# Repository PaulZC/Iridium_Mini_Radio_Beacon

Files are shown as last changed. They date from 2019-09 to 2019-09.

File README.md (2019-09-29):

# Iridium_Mini_Radio_Beacon

An 80g version of the [Iridium 9603N Beacon](https://github.com/PaulZC/Iridium_9603_Beacon) with eRIC4/9 radio support
.

Suitable for high altitude ballooning and many other asset tracking applications.

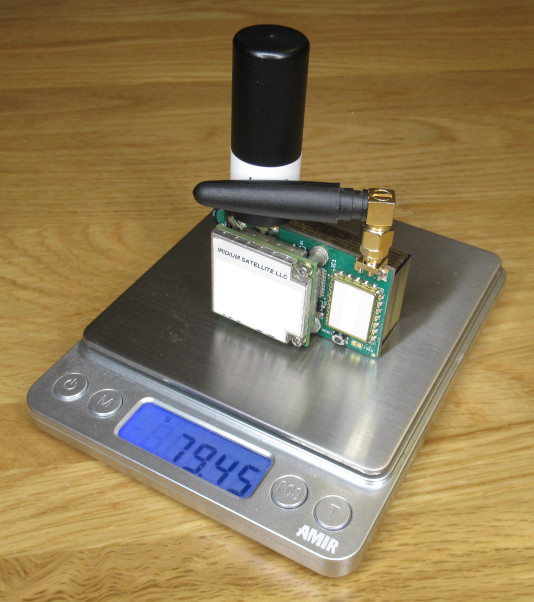
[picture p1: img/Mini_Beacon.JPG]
Mini_Beacon


This version is powered by a single Energiser® Ultimate Lithium L522 (PP3) 9V battery, which helps keep the design as compact as possible.

If you want to keep the size and weight as low as possible, and don't need a radio link, have a look at
the [Iridium 9603N Mini Beacon](https://github.com/PaulZC/Iridium_9603N_Mini_Beacon) instead.

The Iridium 9603N transceiver and u-blox MAX-M8Q GNSS receiver share a single Maxtena M1600HCT-P-SMA antenna, again to keep the weight as low as possible.
The antenna sharing circuit has been flight tested on the [Iridium 9603N Solar Beacon](https://github.com/PaulZC/Iridium_9603N_Solar_Beacon).

Full details of how to track your beacon via the Rock7 RockBLOCK Gateway are included in the
[Iridium 9603N Beacon repo](https://github.com/PaulZC/Iridium_9603_Beacon/blob/master/RockBLOCK.md).

[ASSEMBLY.md](https://github.com/PaulZC/Iridium_Mini_Radio_Beacon/blob/master/ASSEMBLY.md) describes how to assemble the PCB.

The [Arduino folder](https://github.com/PaulZC/Iridium_Mini_Radio_Beacon/tree/master/Arduino) contains the code for the SAMD21 processor.
You can find the [programming instructions](https://github.com/PaulZC/Iridium_9603_Beacon/blob/master/LEARN.md#how-do-i-install-the-atsamd21g18-bootloader)
and [upload instructions](https://github.com/PaulZC/Iridium_9603_Beacon/blob/master/LEARN.md#how-do-i-upload-the-arduino-code) in the Iridium 9603N Beacon repo.

The Eagle files are available in the [Eagle folder](https://github.com/PaulZC/Iridium_Mini_Radio_Beacon/tree/master/Eagle).

The schematic, dimensions and BOM are available [here](https://github.com/PaulZC/Iridium_Mini_Radio_Beacon/blob/master/Iridium_Mini_Radio_Beacon.pdf).

The [OpenSCAD folder](https://github.com/PaulZC/Iridium_Mini_Radio_Beacon/tree/master/OpenSCAD) contains .scad and .stl files for the 3D-printed cover.

## Licence

This project is distributed under a Creative Commons Attribution + Share-alike (BY-SA) licence.
Please refer to section 5 of the licence for the "Disclaimer of Warranties and Limitation of Liability".

Enjoy!

**_Paul_**

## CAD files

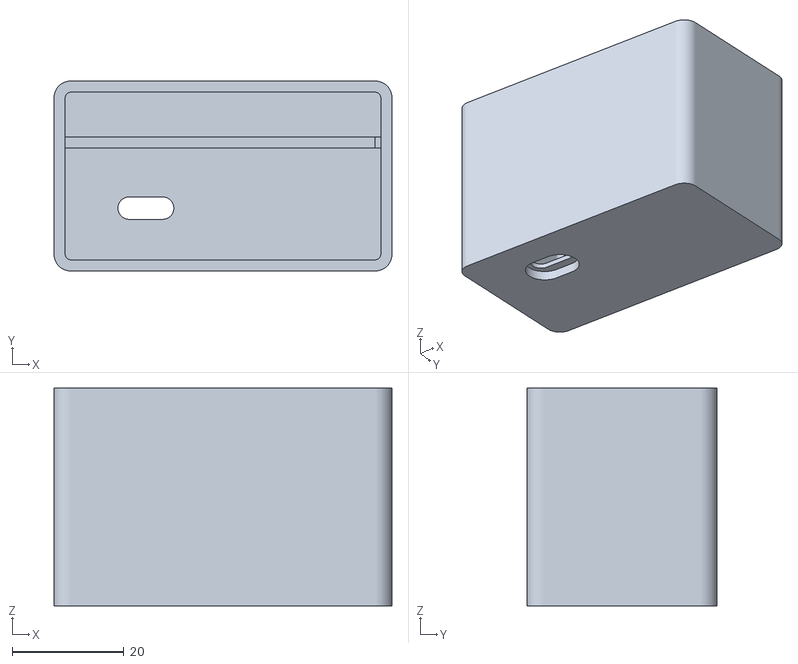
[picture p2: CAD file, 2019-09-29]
OpenSCAD/Mini_Radio_Beacon_Cover.stl
60.5 x 34.0 x 39.0

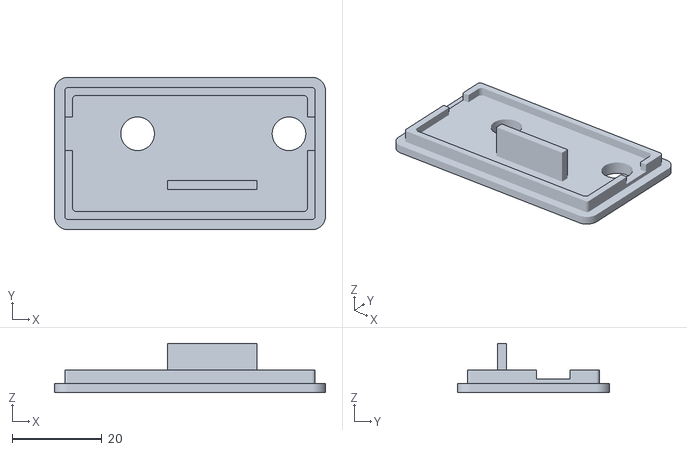
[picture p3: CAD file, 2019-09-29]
OpenSCAD/Mini_Radio_Beacon_Lid.stl
60.5 x 34.0 x 11.0

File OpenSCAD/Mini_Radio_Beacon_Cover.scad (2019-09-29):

// Simple Cover for the Iridium Mini Radio Beacon with USB opening

$fn=90; // fragments
wall = 2.0; // wall thickness
end_wall = 3.0; // end wall thickness
internal_width = 56.5; // internal width (X) of the cover
internal_depth = 30.0; // internal depth (Y) of the cover
internal_height = 35.0; // internal height (Z) of the cover
lid_insert = 1.0; // extra height for the lid insert

battery_support_height = 1.0; // Height (Z) of the battery support above the floor
battery_support_depth = 2.0; // Depth (Y) of the battery support
battery_support_offset = 5.0; // Y offset of the battery support

battery_support_2_width = 1.0; // Width (X) of the battery support from the wall
battery_support_2_height = 27.0; // Internal height (Z) of the battery support

internal_corner_radius = 1.0; // radius of the internal corner cylinder

usb_r = 2.0; // radius of the opening for the USB connector
usb_width = 10.0; // total width of the opening for the USB
usb_height = 1.0; // thickness of the opening for the USB connector
usb_recess_r = 4.0; // radius of the recess for the USB connector body
usb_recess_width = 12.0; // total width of the recess for the USB connector body
usb_x_offset = -13.8; // X offset of the USB connector
usb_y_offset = 5.75; // y offset of the USB connector

height = internal_height + end_wall + lid_insert; // cover external height (Z)
width = internal_width + (2 * wall); // cover external width (X)
depth = internal_depth + (2 * wall); // cover external depth (Y)

external_corner_radius = internal_corner_radius + wall; // external corner radius

module cover()
{
    translate([external_corner_radius, external_corner_radius, 0])
        minkowski() {
            cube([(width - (2 * external_corner_radius)), (depth - (2 * external_corner_radius)), (height / 2)]);
            cylinder(h=(height / 2), r=external_corner_radius);
        }
}

module void()
// Void will be higher than required to avoid zero thickness skin across opening
{
    translate([external_corner_radius, external_corner_radius, end_wall])
        minkowski() {
            cube([(internal_width - (2 * internal_corner_radius)), (internal_depth - (2 * internal_corner_radius)), (height / 2)]);
            cylinder(h=(height / 2), r=internal_corner_radius);
        }
}

module usb_opening_end_1()
// Cylinder is taller than it needs to be to avoid zero thickness skins
{
    translate([((usb_width / 2) - usb_r),0,usb_height]) {
        cylinder(h=end_wall,r=usb_r);
    }
}

module usb_opening_end_2()
// Cylinder is taller than it needs to be to avoid zero thickness skins
{
    translate([(0-((usb_width / 2) - usb_r)),0,usb_height]) {
        cylinder(h=end_wall,r=usb_r);
    }
}

module usb_opening_mid()
// Cube is taller than it needs to be to avoid zero thickness skins
{
    translate([(-0.5 * (usb_width - (2 * usb_r))), (-0.5 * (2 * usb_r)), usb_height]) {
        cube([(usb_width - (2 * usb_r)), (2 * usb_r), end_wall]);
    }
}

module usb_recess_end_1()
// Cylinder is taller than it needs to be to avoid zero thickness skins
{
    translate([((usb_recess_width / 2) - usb_recess_r), 0, (0 - usb_height)]) {
        cylinder(h=end_wall, r=usb_recess_r);
    }
}

module usb_recess_end_2()
// Cylinder is taller than it needs to be to avoid zero thickness skins
{
    translate([(0-((usb_recess_width / 2) - usb_recess_r)), 0, (0 - usb_height)]) {
        cylinder(h=end_wall, r=usb_recess_r);
    }
}

module usb_recess_mid()
// Cube is taller than it needs to be to avoid zero thickness skins
{
    translate([(-0.5 * (usb_recess_width - (2 * usb_recess_r))), (-0.5 * (2 * usb_recess_r)), (0 - usb_height)]) {
        cube([(usb_recess_width - (2 * usb_recess_r)), (2 * usb_recess_r), end_wall]);
    }
}

module usb()
{
    translate([((width / 2) + usb_x_offset), ((depth / 2) - usb_y_offset), 0]) {
        union() {
            usb_opening_end_1();
            usb_opening_end_2();
            usb_opening_mid();
            usb_recess_end_1();
            usb_recess_end_2();
            usb_recess_mid();
        }
    }
}

module battery_support()
{
    translate([0, ((depth/2) + battery_support_offset), 0]) {
        cube([width, battery_support_depth, (end_wall + battery_support_height)]);
    }
}

module battery_support_2()
{
    translate([(width - (wall + battery_support_2_width)), ((depth/2) + battery_support_offset), 0]) {
        cube([(wall + battery_support_2_width), battery_support_depth, (end_wall + battery_support_2_height)]);
    }
}

module finished_cover()
{
    union() {
        difference() {
            cover();
            void();
            usb();
        }
        battery_support();
        battery_support_2();
    }
}

finished_cover();

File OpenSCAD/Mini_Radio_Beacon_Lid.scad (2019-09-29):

// Simple Lid for the Iridium Mini Radio Beacon Cover

$fn=90; // fragments
wall = 2.0; // cover wall thickness
thickness = 2.0; // lid end thickness
internal_width = 56.5; // internal width (X) of the cover
internal_depth = 30.0; // internal depth (Y) of the cover
gap = 0.3; // clearance gap (per side)
insert_height = 3.0; // extra height for the lid insert
internal_corner_radius = 1.0; // radius of the internal corner cylinder

sma_r = 3.75; // radius of the hole for the sma connector
sma_x_offset = -11.7; // X offset of the hole for the sma connector w.r.t. the X center of the void
sma_y_offset = 4.4; // y offset of the hole for the sma connector w.r.t. the Y center of the void
sma_wall_thickness = 3.0; // wall thickness around the SMA connectors

sma_2_x_offset = 22.1; // X offset of the hole for the second sma connector w.r.t. the X center of the void

battery_support_width = 20.0; // Width (X) of the battery support
battery_support_depth = 2.0; // Depth (Y) of the battery support
battery_support_insertion = 9.0; // Insertion height (Z) from cover lip
battery_support_x_offset = 5.0;
battery_support_y_offset = -7.0;

if (gap > internal_corner_radius) echo("Error! Gap cannot be greater than the internal corner radius!");

width = internal_width + (2 * wall); // lid external width (X)
depth = internal_depth + (2 * wall); // lid external depth (Y)

total_height = wall + insert_height; // total height of the lid

sma_x = (width / 2) + sma_x_offset; // x position of the sma connector
sma_y = (depth / 2) + sma_y_offset; // y position of the sma connector

sma_2_x = (width / 2) + sma_2_x_offset; // x position of the second sma connector

external_corner_radius = internal_corner_radius + wall; // external corner radius

module outer()
{
    translate([external_corner_radius, external_corner_radius, 0])
        minkowski() {
            cube([(width - (2 * external_corner_radius)), (depth - (2 * external_corner_radius)), (thickness / 2)]);
            cylinder(h=(thickness / 2), r=external_corner_radius);
        }
}

module inner()
// Thicker than required to avoid zero thickness joints
{
    translate([external_corner_radius, external_corner_radius, 0])
        minkowski() {
            cube([(width - (2 * external_corner_radius)), (depth - (2 * external_corner_radius)), (total_height / 2)]);
            cylinder(h=(total_height / 2), r=(internal_corner_radius - gap));
        }
}

module recess()
// Thicker than required to avoid zero thickness joints
{
    translate([(internal_corner_radius + wall + wall), (internal_corner_radius + wall + wall), sma_wall_thickness])
        minkowski() {
            cube([(width - (2 * (wall + wall + internal_corner_radius))), (depth - (2 * (wall + wall + internal_corner_radius))), (total_height / 2)]);
            cylinder(h=(total_height / 2), r=internal_corner_radius);
        }
}

module battery_support()
{
    translate([((width / 2) + battery_support_x_offset - (battery_support_width / 2)), ((depth / 2) + battery_support_y_offset - (battery_support_depth / 2)), 0]) {
        cube([battery_support_width, battery_support_depth, (battery_support_insertion + thickness)]);
    }
}

module lid()
{
    union() {
        outer();
        inner();
     }
}

module sma()
// Cylinder is taller than required to avoid zero thickness skins
{
    translate([sma_x, sma_y, -1]) {
        cylinder(h=(total_height + 2),r=sma_r);
    }
}

module sma_2()
// Cylinder is taller than required to avoid zero thickness skins
{
    translate([sma_2_x, sma_y, -1]) {
        cylinder(h=(total_height + 2),r=sma_r);
    }
}

module pcb_slot()
// Cube is taller amd wider than required to avoid zero thickness skins
{
    translate([0, (sma_y - sma_r), sma_wall_thickness]) {
        cube([width, (sma_r * 2), total_height]);
    }
}

module finished_lid()
{
    union() {
        difference() {
            lid();
            sma();
            sma_2();
            recess();
            pcb_slot();
        }
        battery_support();
    }
}

finished_lid();

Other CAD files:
OpenSCAD/Mini_Radio_Beacon_Cover__No_USB.stl
OpenSCAD/Mini_Radio_Beacon_Cover__No_USB.scad

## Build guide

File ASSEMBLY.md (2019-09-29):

# Iridium Mini Radio Beacon: Assembly

Here are the assembly instructions for the Iridium 9603N Mini Beacon:

### Blank PCB

Start by having the blank PCBs manufactured. If you are based in the UK or Europe, I can recommend
[Multi-CB](https://www.multi-circuit-boards.eu/en/index.html) who can manufacture PCBs in 1-8 working days and
can process the Eagle .brd file direct - there's no need to generate Gerber files.

My recommended options are:
- Layers: 2 layers
- Format: single pieces
- Surface finish: chemical gold (ENIG)
- Material: FR4, 1.55mm
- Cu layers: 35um
- Solder stop: both sides, green
- Marking print: both sides, white

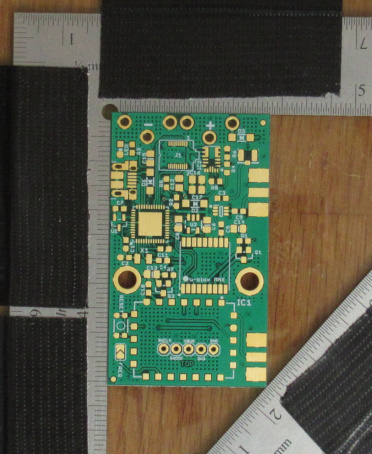
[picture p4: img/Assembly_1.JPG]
Assembly_1


### Add solder paste

Multi-CB can also provide you with a solder paste (SMD) stencil for the PCB. My recommended options are:
- SMD stencil for: top layer
- Make the Y dimension 20mm longer than the PCB itself to allow you to fix it down with tape
- Type: custom
- Pad reduction: yes, 10%
- Thickness: 100um
- Existing fiducials: lasered through
- Text type: half lasered
- Double-sided brushing: yes

I secure the blank PCB onto a flat work surface by locating it between two engineer's squares. I use a sheet of toughened glass
as the work surface as it is both very flat and easy to clean.

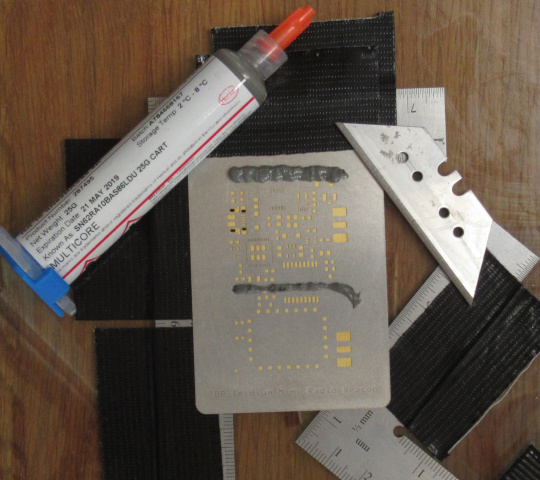
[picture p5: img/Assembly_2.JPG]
Assembly_2


Use the two round fiducials to line up the stencil with the PCB. Secure the stencil with tape.

Apply solder paste close to the component cut-outs and then scrape the paste over the stencil using a knife blade
or a similar straight edge. Take appropriate safety precautions when working with solder paste - particularly if you are using
tin-lead solder instead of lead-free.

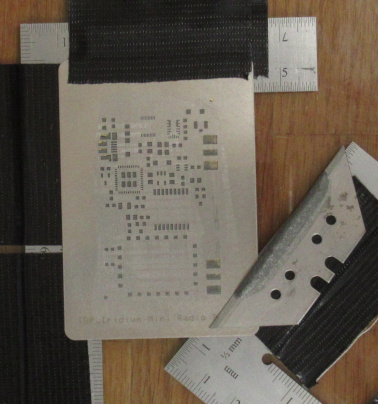
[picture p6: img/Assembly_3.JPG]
Assembly_3


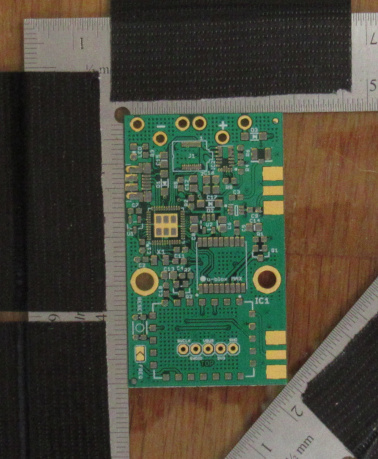
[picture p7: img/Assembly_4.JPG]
Assembly_4


### Position the surface mount components

Position the components onto the blobs of solder paste using tweezers. A magnifier lamp or a USB microscope will
help you place the components in the correct position. J1 - the 20-way Samtec connector - is probably the trickiest
component to position. Take extra time to make sure the legs are centered accurately on the pads.
You may find the [SMT_Component_Placer](https://github.com/PaulZC/SMT_Component_Placer) useful.

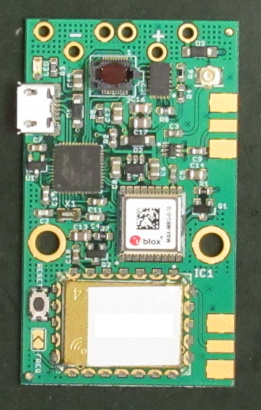
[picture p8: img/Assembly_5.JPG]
Assembly_5


### Reflow the surface mount components

Use a reflow oven to heat the circuit board to the correct temperatures to melt the solder. A reflow oven doesn't need to be
expensive. The one shown below was assembled from:

- Quest 9L 800W mini-oven
- Inkbird PID temperature controller and 40A solid state relay
- Type K thermocouple

Several people have published good reflow oven construction guides, including [this one](http://tt7hab.blogspot.com/2018/06/the-reflow-oven.html)
and [this one](http://www.die4laser.com/toaster/index.html).

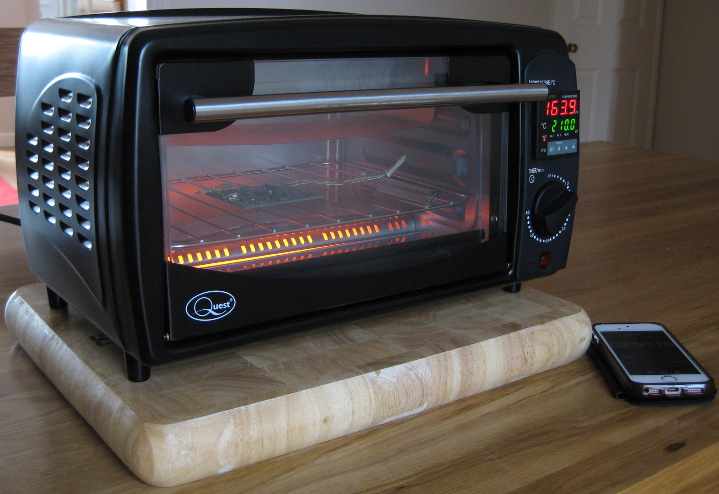
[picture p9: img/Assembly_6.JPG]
Assembly_6


Use the correct temperature profile for your solder paste, but you won't go far wrong with 160C for four minutes, followed by
210C for one minute, followed by a cool-down with the door open. Use a flashlight to check that the solder has melted across
the whole PCB at 210C. Hold the temperature at 210C a little longer if some of the solder paste still appears 'gray' instead of 'silver'.

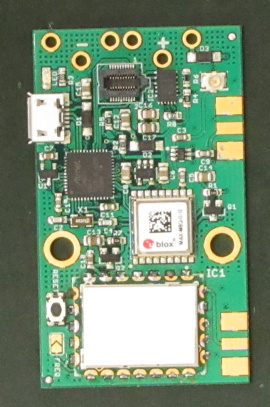
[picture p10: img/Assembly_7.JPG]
Assembly_7


### Check for shorts

Carefully examine all the solder joints and correct any shorts you find.

The 'trick' to removing a short is to add more solder or solder paste and then to use
copper solder braid or wick to remove all the solder in one go.

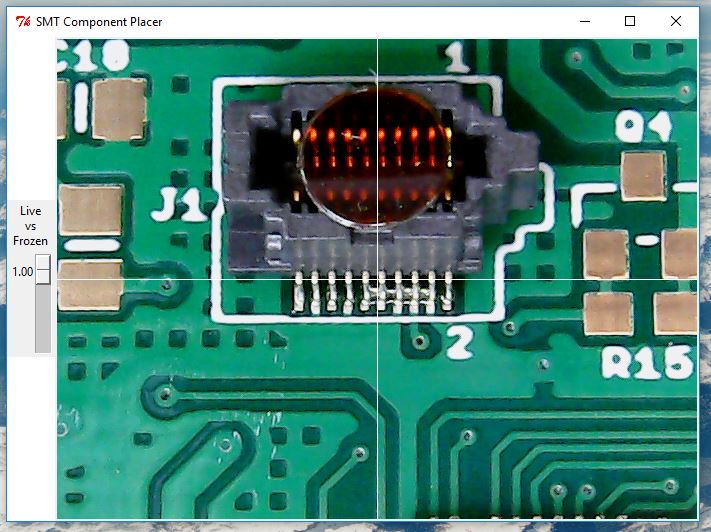
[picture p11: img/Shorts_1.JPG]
Shorts_1


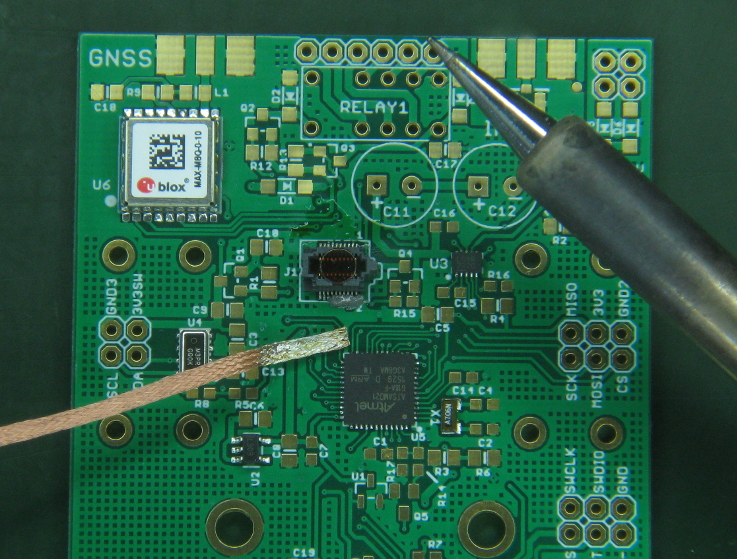
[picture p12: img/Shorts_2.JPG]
Shorts_2


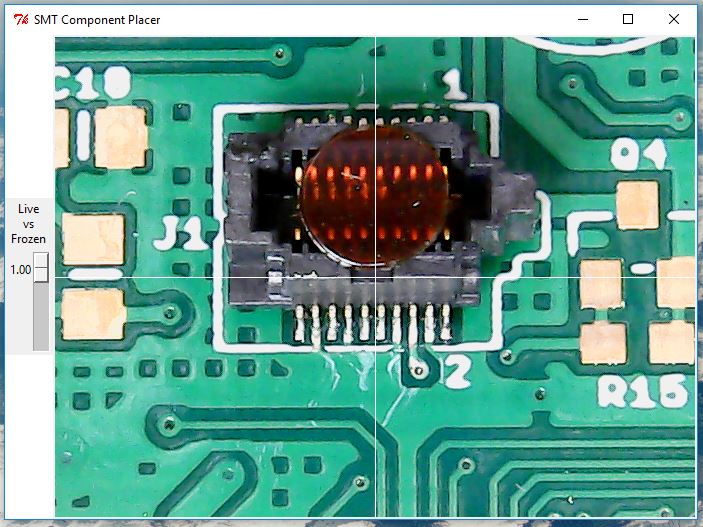
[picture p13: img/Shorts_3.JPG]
Shorts_3


Use a cotton swab dipped in Iso-Propyl Alcohol (IPA / Propanol / rubbing alcohol) to remove any flux residue.

### Press-in nuts

The Iridium 9603N module is held in place by two 2-56 screws. The threaded 2-56 press-in nuts now need to be pressed into the top of the
PCB. These are McMaster part number 95117A411. The nuts are best pressed into place using an arbor press.

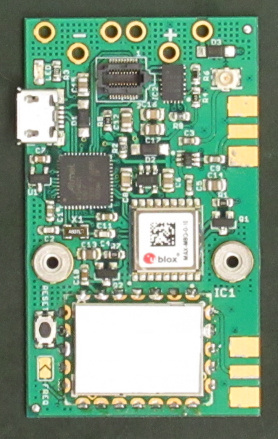
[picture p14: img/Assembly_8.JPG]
Assembly_8


### Add the non-surface mount components

The non-surface mount components (battery clips & SMA connectors) can now be soldered in by hand.

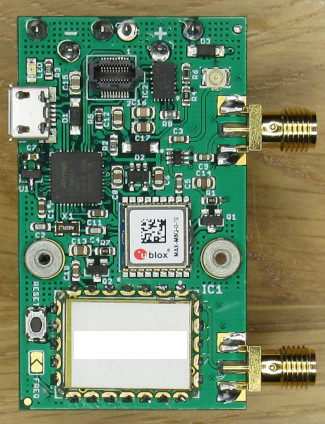
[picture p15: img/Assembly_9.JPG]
Assembly_9


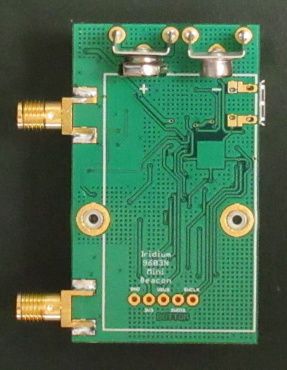
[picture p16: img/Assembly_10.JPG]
Assembly_10


### Install the bootloader

The SAMD21G18A processor now needs to be configured with a bootloader using a J-Link programmer or similar. See
[How do I install the ATSAMD21G18 Bootloader](https://github.com/PaulZC/Iridium_9603N_Solar_Beacon/blob/master/LEARN.md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)
for further details.

### Install the Iridium 9603N module

Take appropriate ESD precautions throughout and especially when handling the 9603N module.

Connect the 9603N to the beacon PCB using a HIROSE (HRS) u.FL-u.FL cable or similar. The cable needs to be 50 Ohm and approximately 25mm long.

Carefully fold the 9603N module over onto the PCB, insert the 20-way connector into the Samtec socket, then secure the module using:
- two 1/8" OD x 3/16" spacers (McMaster 92511A127)
- two 2-56 x 3/8" screws (McMaster 92185A079)

Screw the antennas onto the SMA connectors.

Mini_Beacon

### Test the PCB

Test the completed PCB using the [Arduino code](https://github.com/PaulZC/Iridium_Mini_Radio_Beacon/tree/master/Arduino).

### Secure J1 with Epoxy

I recommend securing J1 to the PCB with a small amount of epoxy to make it more robust. 3M Scotch-Weld 2216 is an ideal choice as it remains slightly flexible when cured.
You will need to temporarily remove the 9603N while you apply the epoxy. Apply the mixed epoxy around the body and legs of J1 using a toothpick,
taking great care to keep the epoxy clear of the connector opening and pins. Make sure the epoxy is fully cured before re-installing the 9603N.

### Lacquer the PCB

I recommend giving the PCB a coat of lacquer, especially if you are intending to use it to track a balloon flight.
You will need to temporarily remove the 9603N while you apply the lacquer. Cover all of the surface mount components with
[Acrylic Protective Lacquer (conformal coating)](https://uk.rs-online.com/web/p/conformal-coatings/3217324/) except: J1, SW1, CON1, IO pads.
Keep the top of the MAX-M8Q clear of lacquer too as its package is only just thin enough to fit under the 9603N.

Once the lacquer is dry, re-attach the 9603N and your board is ready for use.

### The Small Print

This project is distributed under a Creative Commons Attribution + Share-alike (BY-SA) licence.
Please refer to section 5 of the licence for the "Disclaimer of Warranties and Limitation of Liability".

Enjoy!

**_Paul_**

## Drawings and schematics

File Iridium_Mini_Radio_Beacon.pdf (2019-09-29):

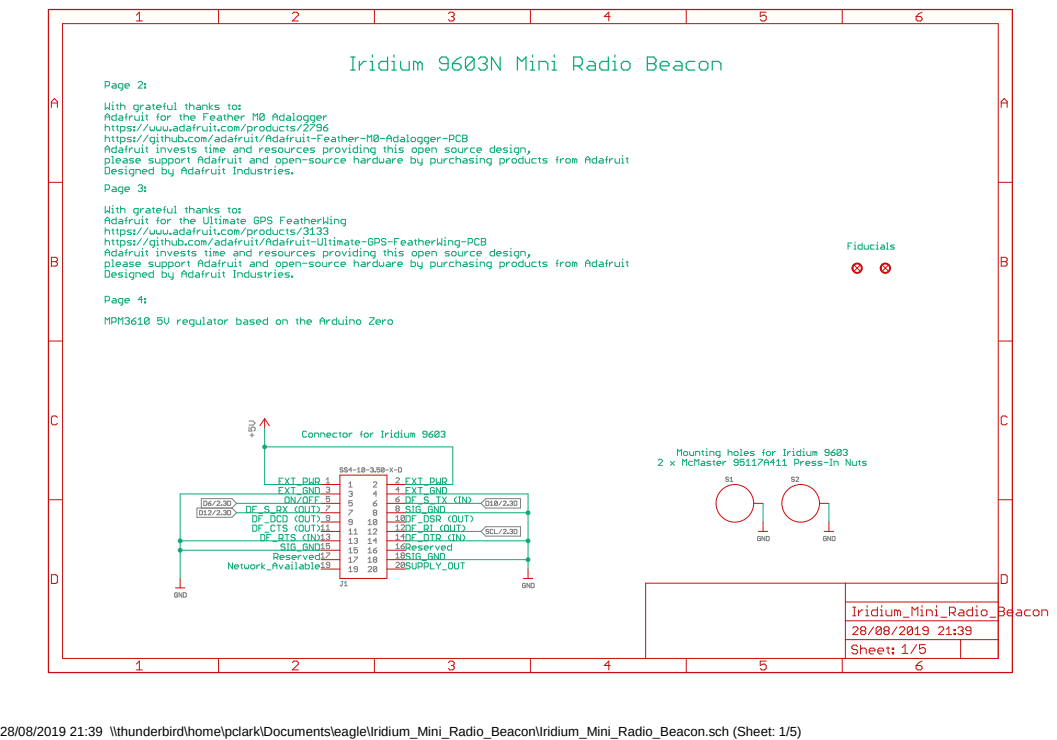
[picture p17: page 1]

28/08/2019 21:39 \\thunderbird\home\pclark\Documents\eagle\Iridium_Mini_Radio_Beacon\Iridium_Mini_Radio_Beacon.sch (Sheet: 1/5)

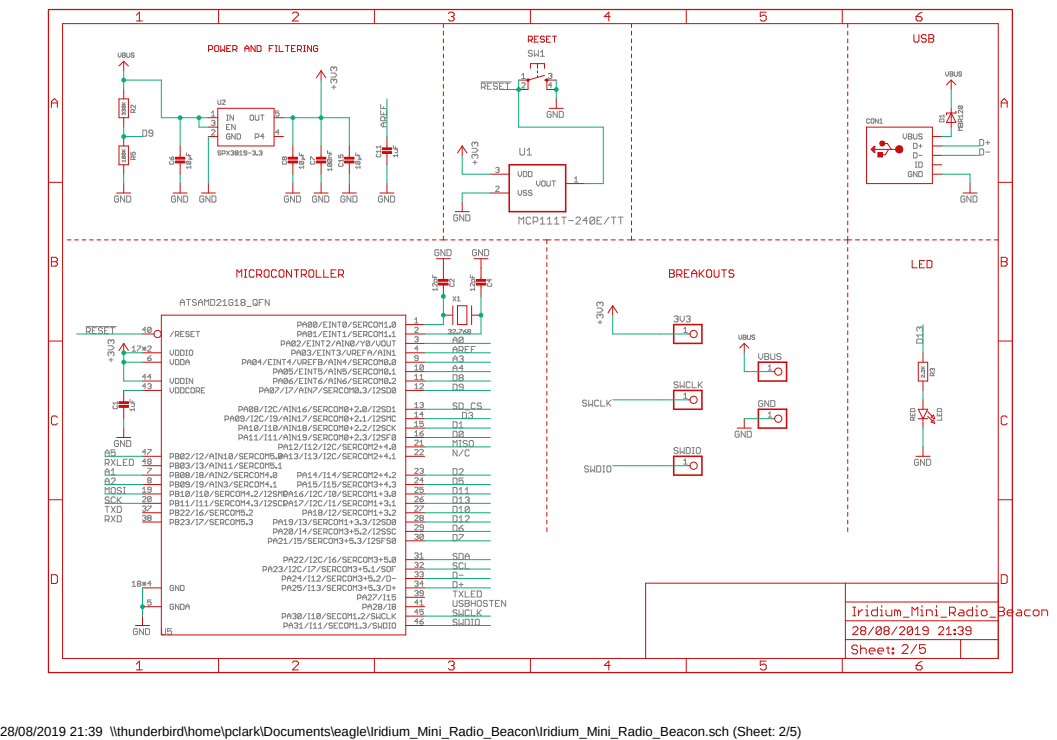
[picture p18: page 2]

28/08/2019 21:39 \\thunderbird\home\pclark\Documents\eagle\Iridium_Mini_Radio_Beacon\Iridium_Mini_Radio_Beacon.sch (Sheet: 2/5)

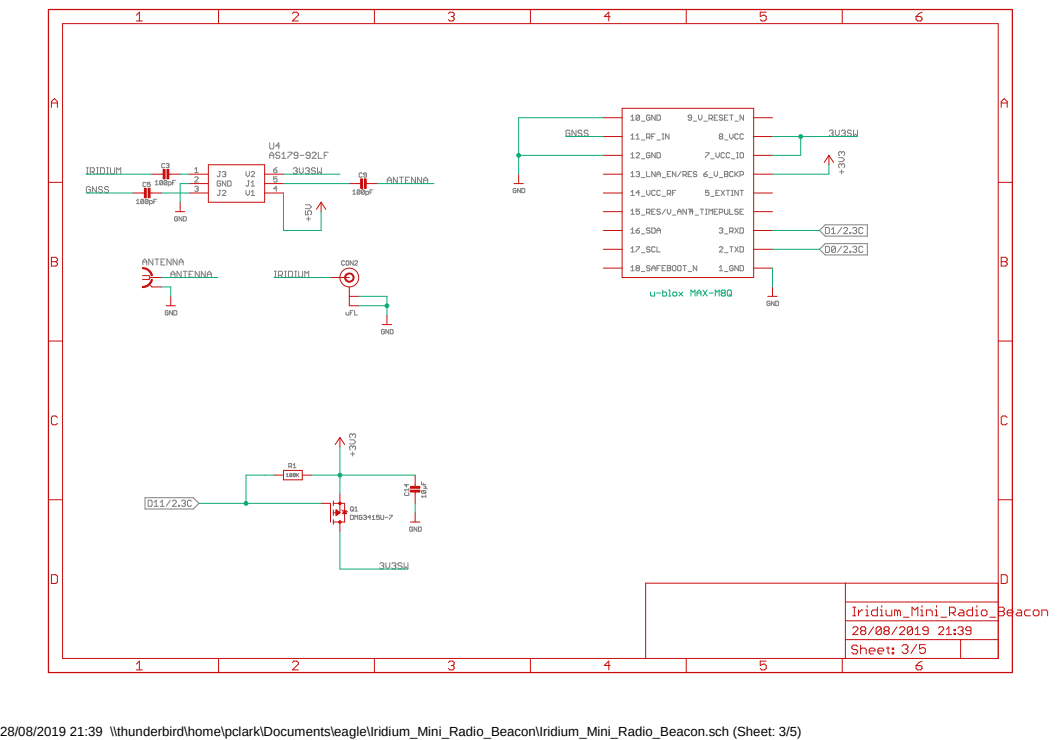
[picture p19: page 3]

28/08/2019 21:39 \\thunderbird\home\pclark\Documents\eagle\Iridium_Mini_Radio_Beacon\Iridium_Mini_Radio_Beacon.sch (Sheet: 3/5)

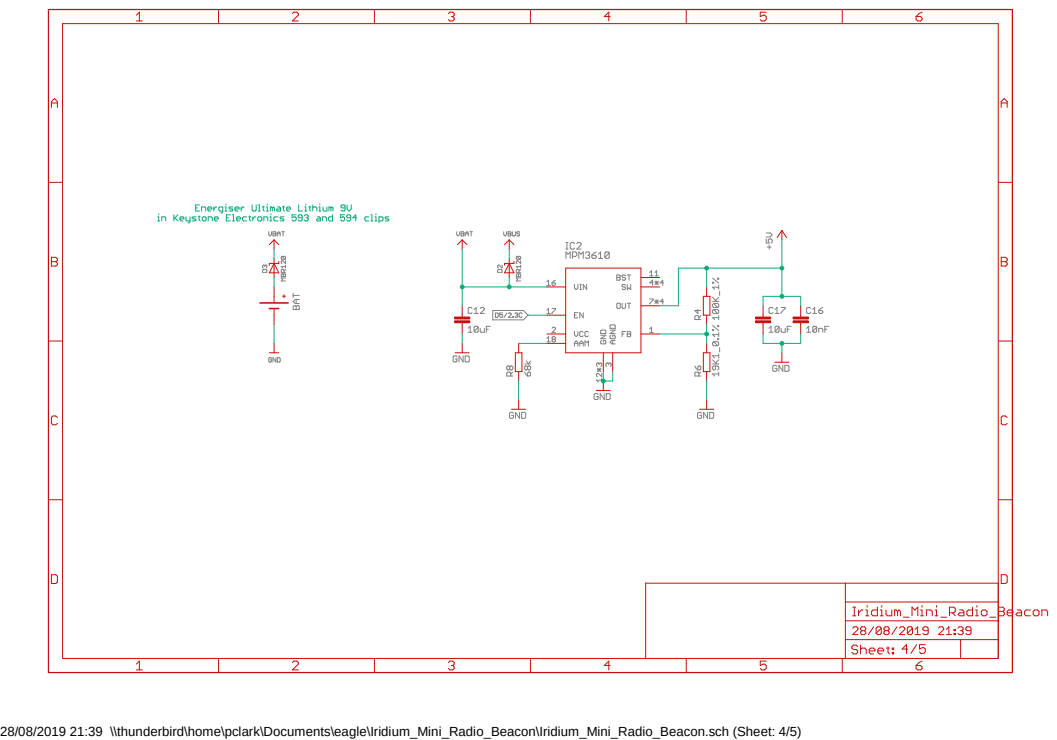
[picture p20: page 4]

28/08/2019 21:39 \\thunderbird\home\pclark\Documents\eagle\Iridium_Mini_Radio_Beacon\Iridium_Mini_Radio_Beacon.sch (Sheet: 4/5)

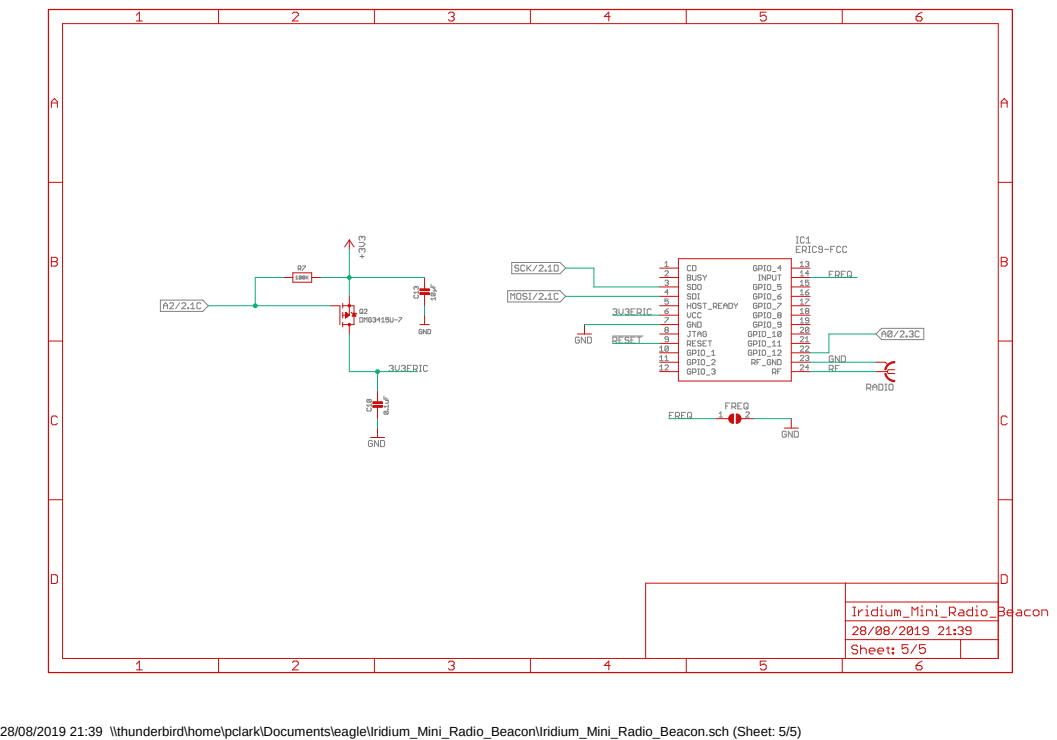
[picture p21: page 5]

28/08/2019 21:39 \\thunderbird\home\pclark\Documents\eagle\Iridium_Mini_Radio_Beacon\Iridium_Mini_Radio_Beacon.sch (Sheet: 5/5)

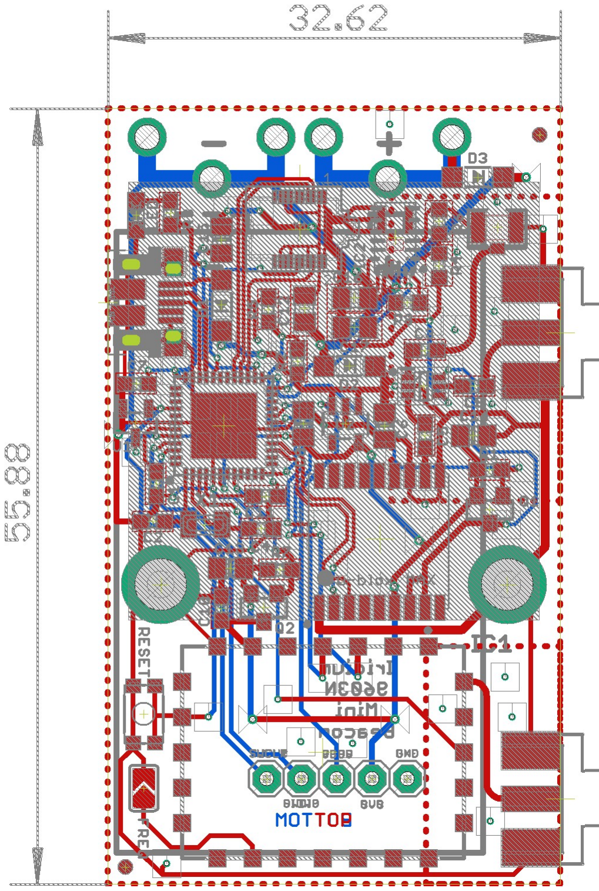
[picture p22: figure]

28/08/2019 18:07 \\thunderbird\home\pclark\Documents\eagle\Iridium_Mini_Radio_Beacon\Iridium_Mini_Radio_Beacon.brd

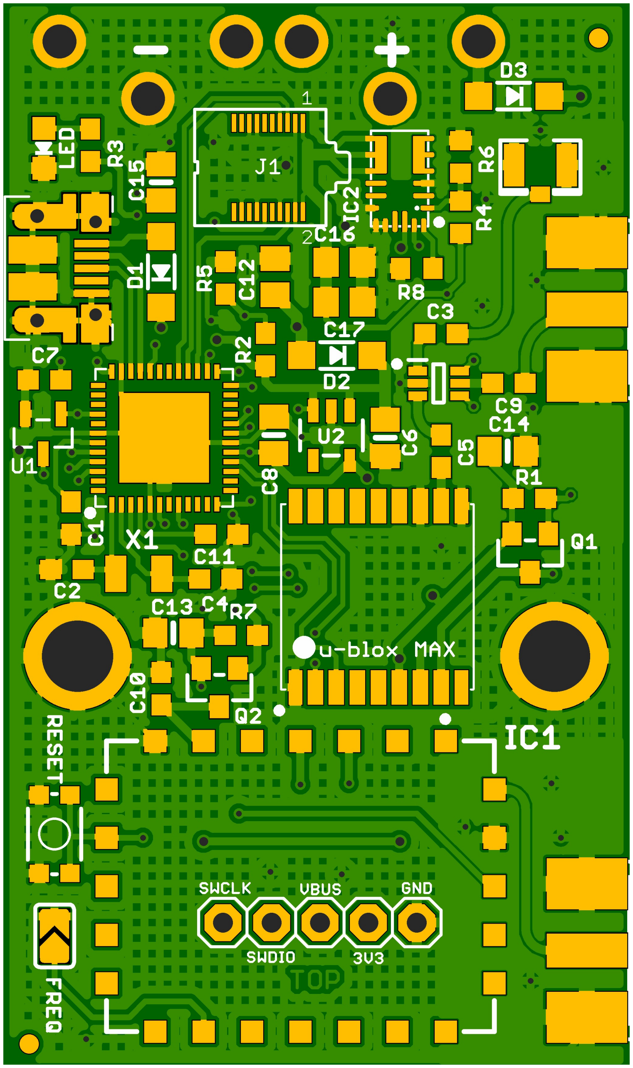
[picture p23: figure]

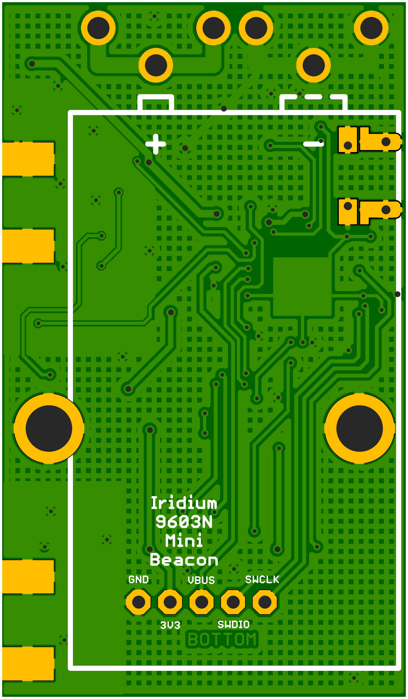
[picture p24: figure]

Part | X | Y | Angle Package | Value | Manufacturer | Manufacturer Part No

Farnell
Part No Mouser Part No

McMaster
Part No Description

Dimensions 32.62 55.88

Fiducials - for solder paste mask alignment:

FD1 | 1.27 | -16.51 0 | Fiducial 1mm
FD2 | 31.12 36.20 0 | Fiducial 1mm

Surface Mount Components:

C1 | 3.46 | 11.05 270 | 0603 | 1uF | Walsin | 0603X105K100CT | 2496916 | MultiLayer Ceramic Capacitor; 1uF; 10V; 0603; X5R
C2 | 3.24 | 8.35 | 180 | 0603 | 12pF | Walsin | 0603N120J500CT | 2496884 | MultiLayer Ceramic Capacitor; 12pF; 50V; 0603
C3 | 22.86 20.7 | 0 | 0603 | 120pF | Walsin | 0603B121K500CT | 2524820 | MultiLayer Ceramic Capacitor; 120pF; 50V; 0603
C4 | 11.05 7.84 | 0 | 0603 | 12pF | Walsin | 0603N120J500CT | 2496884 | MultiLayer Ceramic Capacitor; 12pF; 50V; 0603
C5 | 22.86 14.54 270 | 0603 | 120pF | Walsin | 0603B121K500CT | 2524820 | MultiLayer Ceramic Capacitor; 120pF; 50V; 0603
C6 | 19.94 15.24 270 | 0805 | 10µF | Walsin | 0805F106Z100CT | 2496998 | MultiLayer Ceramic Capacitor; 10uF; 10V; 0805
C7 | 2.06 | 18.29 180 | 0603 | 100nF | Murata | GRM188R71H104JA93D 2688523 | MultiLayer Ceramic Capacitor; 0.1uF; 50V; 0603; X7R
C8 | 14.1 | 15.4 | 90 | 0805 | 10µF | Walsin | 0805F106Z100CT | 2496998 | MultiLayer Ceramic Capacitor; 10uF; 10V; 0805
C9 | 26.42 18.1 | 180 | 0603 | 120pF | Walsin | 0603B121K500CT | 2524820 | MultiLayer Ceramic Capacitor; 120pF; 50V; 0603
C10 | 8.19 | 2.1 | 90 | 0603 | 100nF | Murata | GRM188R71H104JA93D 2688523 | MultiLayer Ceramic Capacitor; 0.1uF; 50V; 0603; X7R
C11 | 11.37 10.19 0 | 0603 | 1uF | Walsin | 0603X105K100CT | 2496916 | MultiLayer Ceramic Capacitor; 1uF; 10V; 0603; X5R
C12 | 14.16 23.69 90 | 0805 | 10µF | Walsin | 0805F106Z100CT | 2496998 | MultiLayer Ceramic Capacitor; 10uF; 10V; 0805
C13 | 8.83 | 5.02 | 180 | 0805 | 10µF | Walsin | 0805F106Z100CT | 2496998 | MultiLayer Ceramic Capacitor; 10uF; 10V; 0805
C14 | 26.35 14.54 0 | 0805 | 10µF | Walsin | 0805F106Z100CT | 2496998 | MultiLayer Ceramic Capacitor; 10uF; 10V; 0805
C15 | 8.19 | 28.64 90 | 0805 | 10µF | Walsin | 0805F106Z100CT | 2496998 | MultiLayer Ceramic Capacitor; 10uF; 10V; 0805
C16 | 17.78 24.45 0 | 0805 | 10nF | Walsin | 0805B103K500CT | 2496939 | MultiLayer Ceramic Capacitor; 10nF; 50V; 0805; X7R
C17 | 17.78 22.35 0 | 0805 | 10µF | Walsin | 0805F106Z100CT | 2496998 | MultiLayer Ceramic Capacitor; 10uF; 10V; 0805
CON1 | 2.99 | 24.13 270 | Micro_USB | Amphenol_FCI | 10103594 | 2293752 | Amphenol FCI 10103594 Micro USB Type B
CON2 | 28.07 28.77 270 | uFL | uFL | Hirose | U.FL-R-SMT(01) | 3908021 | HIROSE U.FL-R-SMT(01); U.FL Coaxial; Straight Jack; 50 ohm
D1 | 8.19 | 23.94 90 | SOD-123 | MBR120 | ON SEMICONDUCTOR MBR120VLSFT1G | 1431044 | Schottky Rectifier; 20V; 1A; SOD-123
D2 | 17.4 | 19.56 180 | SOD-123 | MBR120 | ON SEMICONDUCTOR MBR120VLSFT1G | 1431044 | Schottky Rectifier; 20V; 1A; SOD-123
D3 | 26.67 33.15 180 | SOD-123 | MBR120 | ON SEMICONDUCTOR MBR120VLSFT1G | 1431044 | Schottky Rectifier; 20V; 1A; SOD-123
IC1 | 15.49 -8.26 180 | ERIC4 | LPRS | ERIC4 | 2362439 | LPRS easy Radio Intelligent Controller 433MHz
IC2 | 20.7 | 28.65 180 | QFN-20 | MPM3610 | MPS | MPM3610AGQV-P | 946-MPM3610AGQV-P | Switching Voltage Regulator; 21V; 1.2A; DC/DC
J1 | 13.81 29.41 0 | SS4-10-3.50 | Samtec | SS4-10-3.50-L-D-K-TR | 2085336 | Samtec SS4-10-3.50-L-D-K-TR
LED | 2.03 | 30.42 180 | 2.0x1.25 | RED | Wurth Electronik | 150080RS75000 | 2322077 | LED; Red; 20mA; 2V; 2.0x1.25mm
Q1 | 27.53 9.21 | 180 | SOT23 | DMG3415U-7 | Diodes Inc. | DMG3415U-7 | 1843688 | MOSFET; P Channel; SOT23-WIDE
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

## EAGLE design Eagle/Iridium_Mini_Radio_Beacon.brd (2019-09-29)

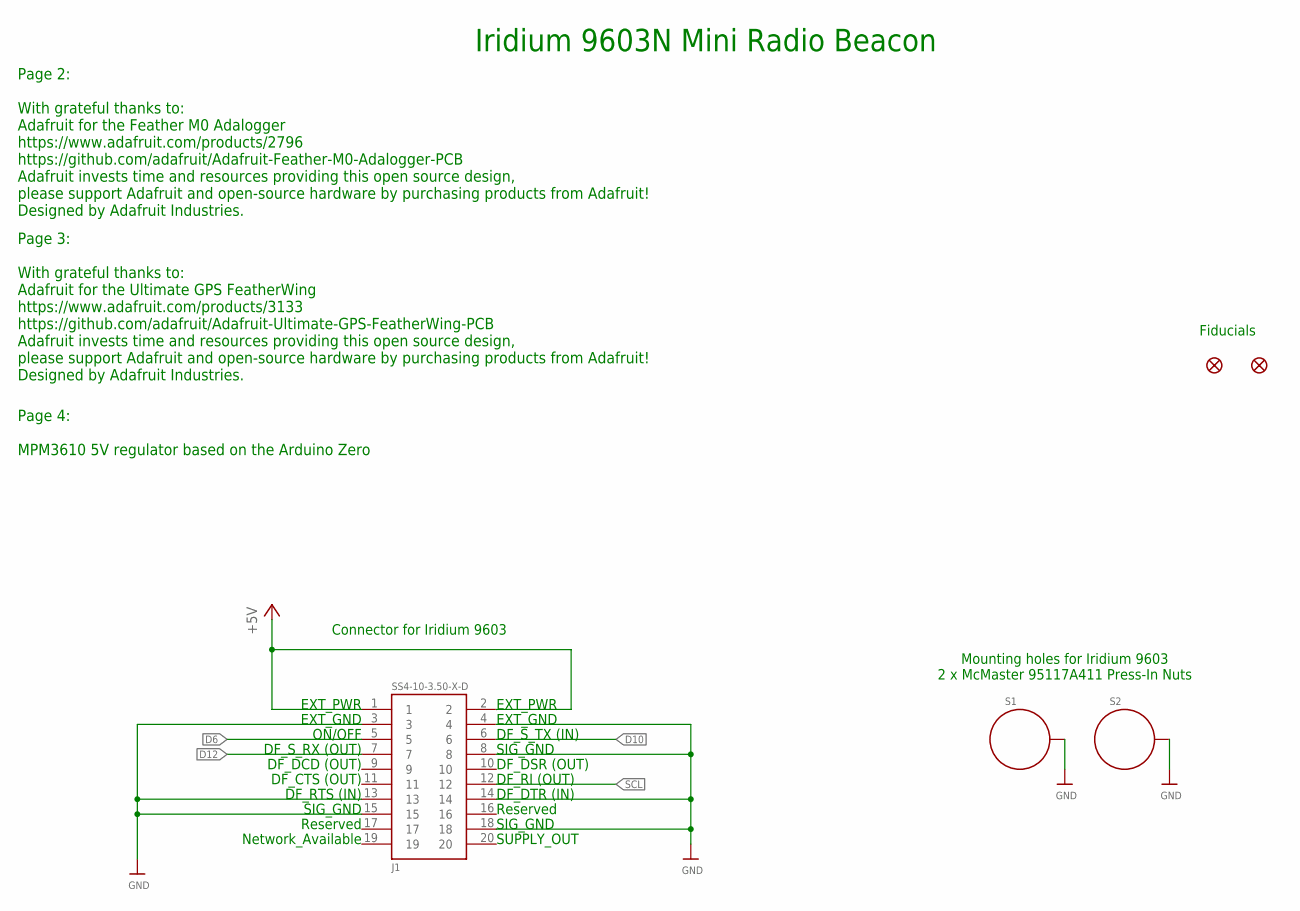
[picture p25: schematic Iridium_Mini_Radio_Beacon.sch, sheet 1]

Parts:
FD1, FD2: FIDUCIAL1X2; FIDUCIAL-1X2
J1: SS4-10-3.50-X-D
S1, S2: STANDOFF_ELECTRICALMCMASTER-95117A411; STANDOFF-ELECTRICAL-MCMASTER-95117A411

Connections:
+5V: J1.1, J1.2; also elsewhere on the board
D6: J1.5; also elsewhere on the board
D10: J1.6; also elsewhere on the board
D12: J1.7; also elsewhere on the board
GND: J1.3, J1.4, J1.8, J1.13, J1.14, J1.15, J1.18, S1.P1, S2.P1; also elsewhere on the board
SCL: J1.12; also elsewhere on the board

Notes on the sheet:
Connector for Iridium 9603
Mounting holes for Iridium 9603 2 x McMaster 95117A411 Press-In Nuts
Iridium 9603N Mini Radio Beacon
Page 2: With grateful thanks to: Adafruit for the Feather M0 Adalogger https://www.adafruit.com/products/2796 https://github.com/adafruit/Adafruit-Feather-M0-Adalogger-PCB Adafruit invests time and resources providing this open source design, please support Adafruit and open-source hardware by purc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
Page 3: With grateful thanks to: Adafruit for the Ultimate GPS FeatherWing https://www.adafruit.com/products/3133 https://github.com/adafruit/Adafruit-Ultimate-GPS-FeatherWing-PCB Adafruit invests time and resources providing this open source design, please support Adafruit and open-source hardware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
EXT_PWR
EXT_GND
ON/OFF
DF_S_RX (OUT)
DF_DCD (OUT)
DF_CTS (OUT)
DF_RTS (IN)
SIG_GND
Reserved
Network_Available
DF_S_TX (IN)
DF_DSR (OUT)
DF_RI (OUT)
DF_DTR (IN)
SUPPLY_OUT
Page 4: MPM3610 5V regulator based on the Arduino Zero
Fiducials

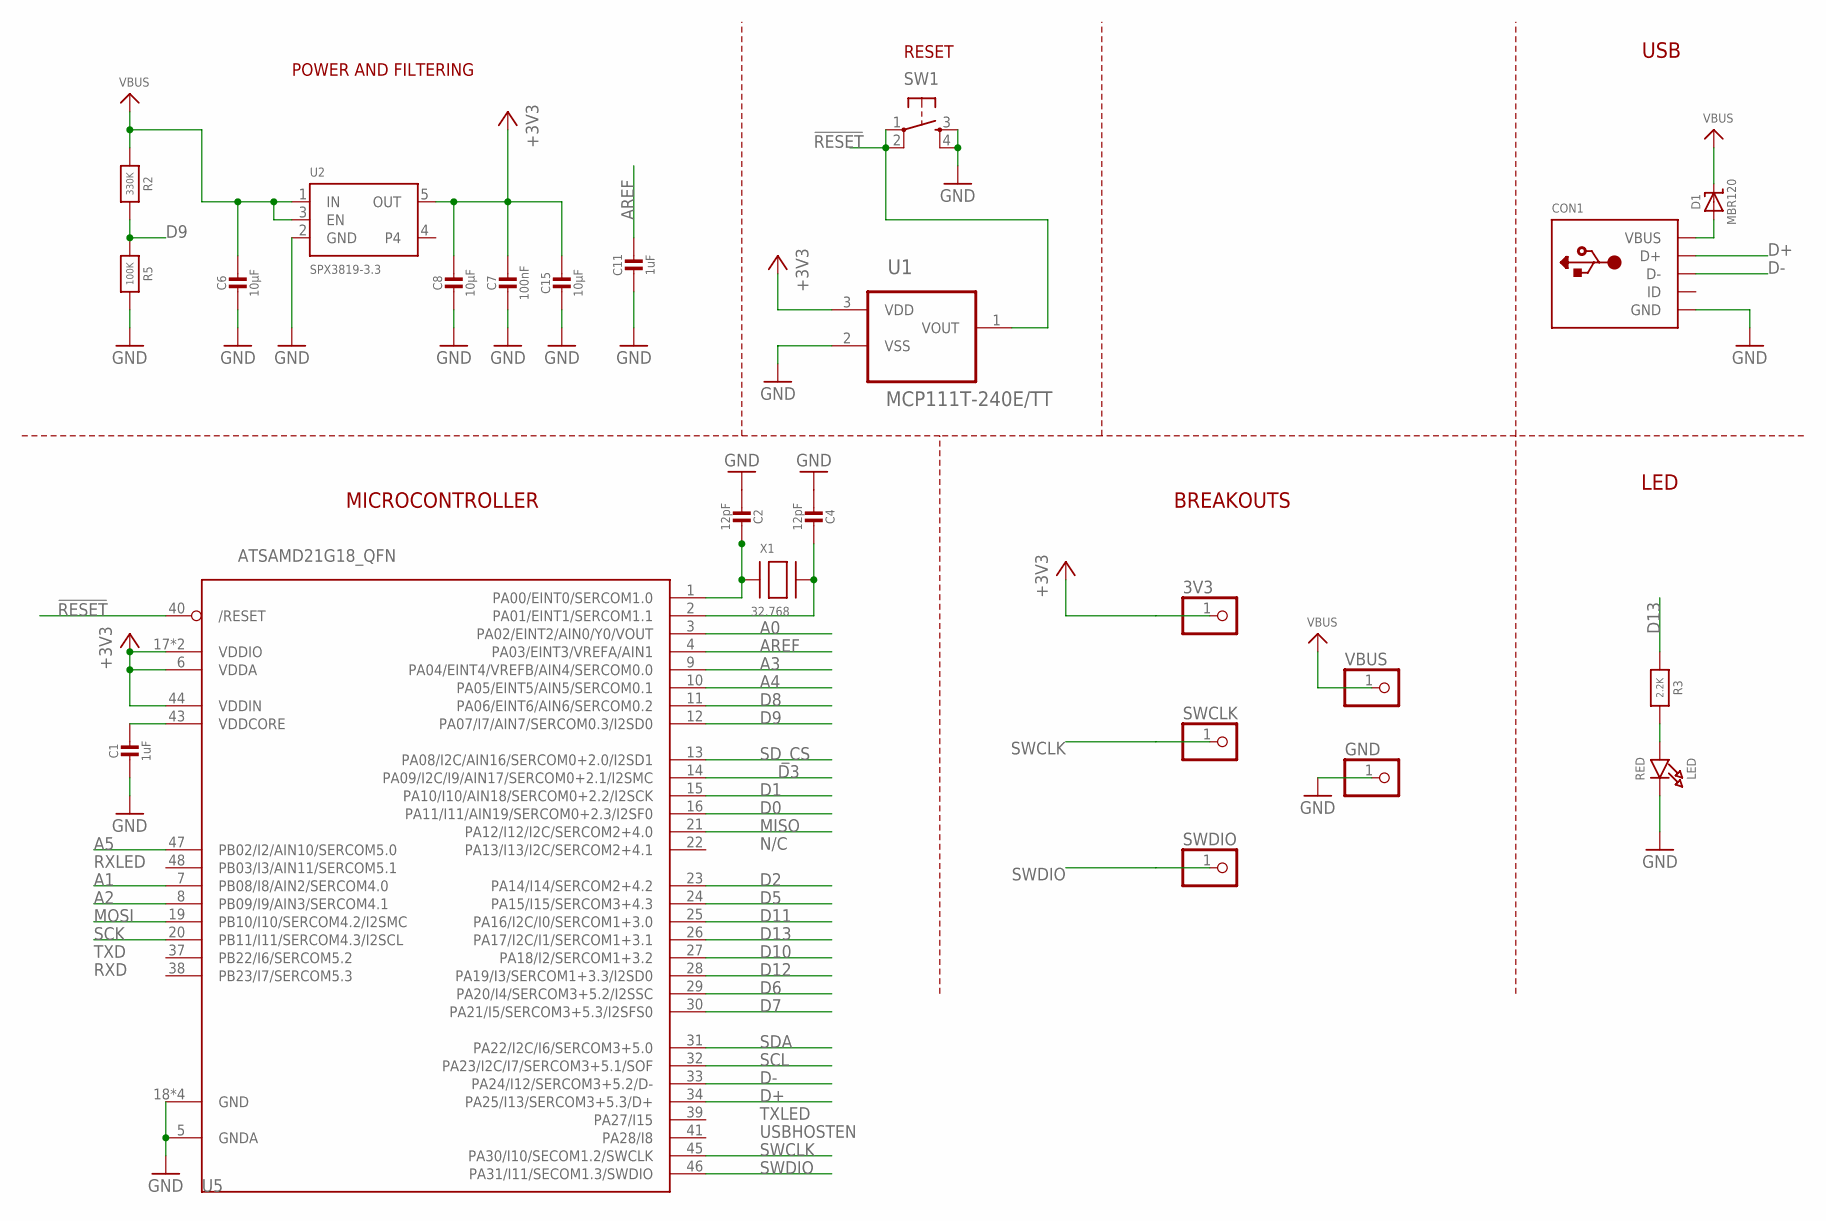
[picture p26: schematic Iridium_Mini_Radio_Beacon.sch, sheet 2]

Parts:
3V3: PINHD-1X1; 1X01
C1, C11: 1uF; 0603-NO
C2, C4: 12pF; 0603-NO
C6, C8, C15: 10µF; 0805-NO
C7: 100nF; 0603-NO
CON1: MICROBUILDER_USBFCI_10103594_CORRECTED; MICROBUILDER_FCI_10103594_CORRECTED
D1: MBR120; SOD-123
GND: PINHD-1X1; 1X01
LED: RED; CHIPLED_0805_NOOUTLINE
R2: 330K; 0603-NO
R3: 2.2K; 0603-NO
R5: 100K; 0603-NO
SW1: SWITCH_SPST_4_PINRECT; TACTILE_SWITCH_SMD_4.6X2.8MM
SWCLK: PINHD-1X1; 1X01
SWDIO: PINHD-1X1; 1X01
U1: MCP111T-240E/TT; SOT95P237X112-3N; MPN MCP111T-240E/TT
U2: SPX3819-3.3; SOT23-5
U5: ATSAMD21G18_QFN; TQFN48_7MM
VBUS: PINHD-1X1; 1X01
X1: 32.768; XTAL3215

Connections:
!RESET: SW1.1, SW1.2, U1.1 (VOUT), U5.40 (/RESET); also elsewhere on the board
+3V3: 3V3.1, C7.1, C8.1, C15.1, U1.3 (VDD), U2.5 (OUT), U5.6 (VDDA), U5.17 (VDDIO), U5.36 (VDDIO), U5.44 (VDDIN); also elsewhere on the board
A0: U5.3 (PA02/EINT2/AIN0/Y0/VOUT); also elsewhere on the board
A1: U5.7 (PB08/I8/AIN2/SERCOM4.0)
A2: U5.8 (PB09/I9/AIN3/SERCOM4.1); also elsewhere on the board
A3: U5.9 (PA04/EINT4/VREFB/AIN4/SERCOM0.0)
A4: U5.10 (PA05/EINT5/AIN5/SERCOM0.1)
A5: U5.47 (PB02/I2/AIN10/SERCOM5.0)
AREF: C11.1, U5.4 (PA03/EINT3/VREFA/AIN1)
D0: U5.16 (PA11/I11/AIN19/SERCOM0+2.3/I2SF0); also elsewhere on the board
D1: U5.15 (PA10/I10/AIN18/SERCOM0+2.2/I2SCK); also elsewhere on the board
D2: U5.23 (PA14/I14/SERCOM2+4.2)
D3: U5.14 (PA09/I2C/I9/AIN17/SERCOM0+2.1/I2SMC)
D5: U5.24 (PA15/I15/SERCOM3+4.3); also elsewhere on the board
D6: U5.29 (PA20/I4/SERCOM3+5.2/I2SSC); also elsewhere on the board
D7: U5.30 (PA21/I5/SERCOM3+5.3/I2SFS0)
D8: U5.11 (PA06/EINT6/AIN6/SERCOM0.2)
D9: R2.2, R5.1, U5.12 (PA07/I7/AIN7/SERCOM0.3/I2SD0)
D10: U5.27 (PA18/I2/SERCOM1+3.2); also elsewhere on the board
D11: U5.25 (PA16/I2C/I0/SERCOM1+3.0); also elsewhere on the board
D12: U5.28 (PA19/I3/SERCOM1+3.3/I2SD0); also elsewhere on the board
D13: R3.1, U5.26 (PA17/I2C/I1/SERCOM1+3.1)
D+: CON1.D+, U5.34 (PA25/I13/SERCOM3+5.3/D+)
D-: CON1.D-, U5.33 (PA24/I12/SERCOM3+5.2/D-)
GND: C1.2, C2.2, C4.2, C6.2, C7.2, C8.2, C11.2, C15.2, CON1.BASE@1 (GND), CON1.BASE@2 (GND), CON1.GND, CON1.SPRT@1 (GND), CON1.SPRT@2 (GND), CON1.SPRT@3 (GND), CON1.SPRT@4 (GND), GND.1, LED.C, R5.2, SW1.3, SW1.4, U1.2 (VSS), U2.2 (GND), U5.5 (GNDA), U5.18 (GND), U5.35 (GND), U5.42 (GND), U5.THERMAL (GND); also elsewhere on the board
MISO: U5.21 (PA12/I12/I2C/SERCOM2+4.0)
MOSI: U5.19 (PB10/I10/SERCOM4.2/I2SMC); also elsewhere on the board
unnamed: LED.A, R3.2
unnamed: C2.1, U5.1 (PA00/EINT0/SERCOM1.0), X1.P$1
unnamed: C4.1, U5.2 (PA01/EINT1/SERCOM1.1), X1.P$2
unnamed: CON1.VBUS, D1.A
SCK: U5.20 (PB11/I11/SERCOM4.3/I2SCL); also elsewhere on the board
SCL: U5.32 (PA23/I2C/I7/SERCOM3+5.1/SOF); also elsewhere on the board
SDA: U5.31 (PA22/I2C/I6/SERCOM3+5.0)
SD_CS: U5.13 (PA08/I2C/AIN16/SERCOM0+2.0/I2SD1)
SWCLK: SWCLK.1, U5.45 (PA30/I10/SECOM1.2/SWCLK)
SWDIO: SWDIO.1, U5.46 (PA31/I11/SECOM1.3/SWDIO)
VBUS: C6.1, D1.C, R2.1, U2.1 (IN), U2.3 (EN), VBUS.1; also elsewhere on the board
VDDCORE1: C1.1, U5.43 (VDDCORE)

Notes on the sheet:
POWER AND FILTERING
RESET
N/C
TXLED
USBHOSTEN
RXLED
TXD
RXD
USB
BREAKOUTS
LED
MICROCONTROLLER

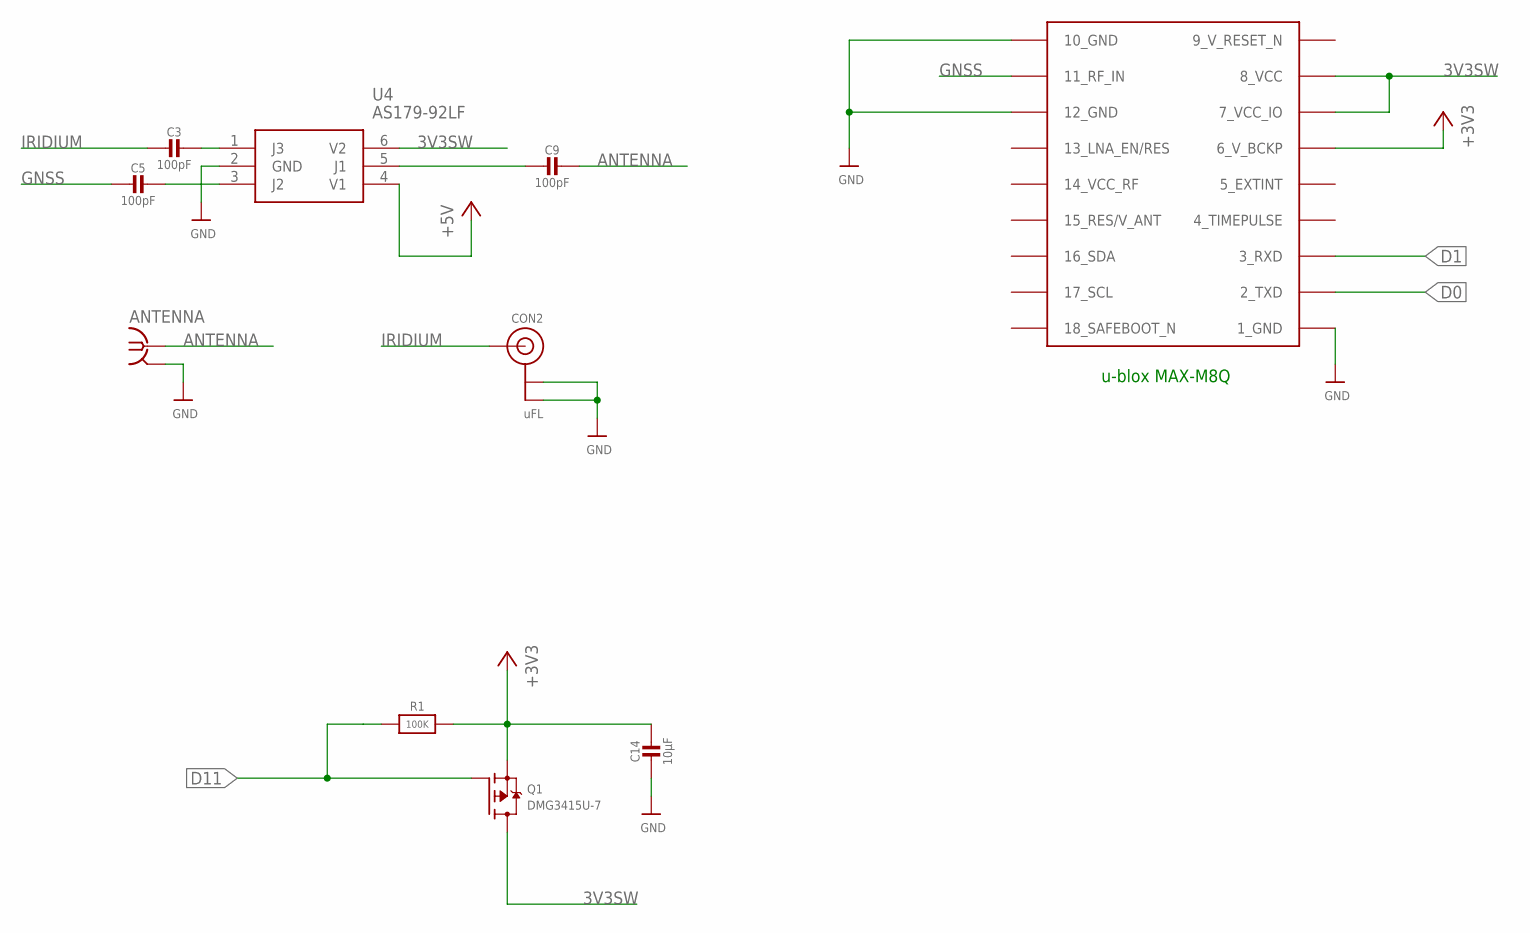
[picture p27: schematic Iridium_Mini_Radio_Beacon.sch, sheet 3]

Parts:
ANTENNA: SMA-142-0711-821/826; J502-ND-142-0711-821/826
C3, C5, C9: 100pF; 0603-NO
C14: 10µF; 0805-NO
CON2: uFL; U.FL
Q1: DMG3415U-7; SOT23-WIDE
R1: 100K; 0603-NO
U3: MAX-M8
U4: AS179-92LF; SOT65P220X100-6N

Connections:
3V3SW: Q1.3 (D), U3.7_VCC_IO, U3.8_VCC, U4.6 (V2)
9_V_RESET_N: U3.9_RESET_N (9_V_RESET_N)
+3V3: C14.1, Q1.2 (S), R1.2, U3.6_V_BCKP; also elsewhere on the board
+5V: U4.4 (V1); also elsewhere on the board
ANTENNA: ANTENNA.1, C9.1
D0: U3.2_TXD; also elsewhere on the board
D1: U3.3_RXD; also elsewhere on the board
D11: Q1.1 (G), R1.1; also elsewhere on the board
GND: ANTENNA.G@1 (2), ANTENNA.G@2 (2), ANTENNA.G@3 (2), ANTENNA.G@4 (2), C14.2, CON2.1 (GND), CON2.2 (GND), U3.1_GND, U3.10_GND, U3.12_GND, U4.2 (GND); also elsewhere on the board
GNSS: C5.2, U3.11_RF_IN
IRIDIUM: C3.2, CON2.3 (SIGNAL)
unnamed: C3.1, U4.1 (J3)
unnamed: C5.1, U4.3 (J2)
unnamed: C9.2, U4.5 (J1)

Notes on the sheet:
u-blox MAX-M8Q

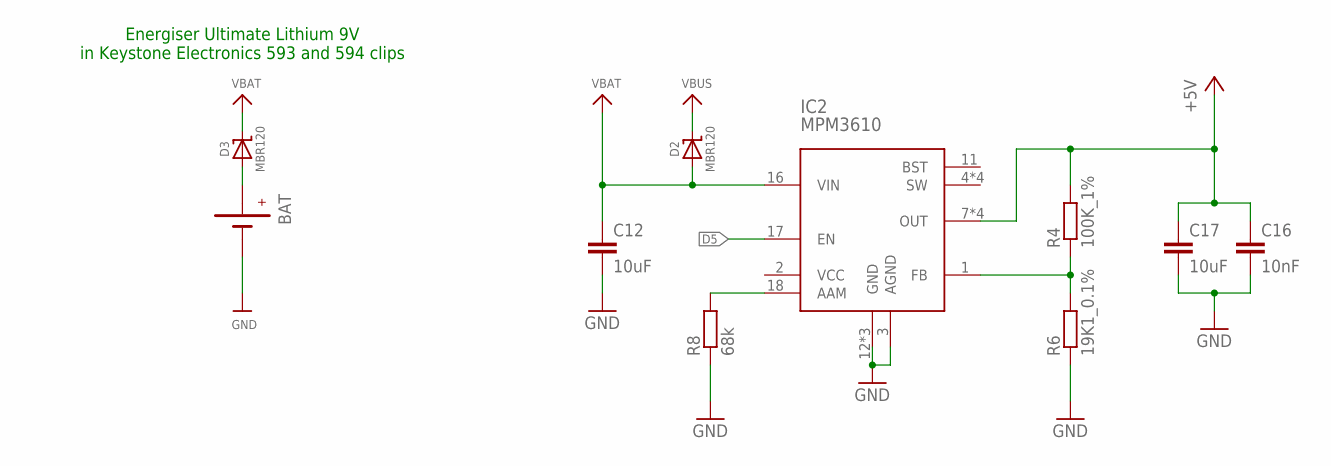
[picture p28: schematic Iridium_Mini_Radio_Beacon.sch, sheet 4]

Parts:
BAT: BATTERYBATTERY-9V-KEYSTONE-593-594-FLIPPED; BATTERY-9V-KEYSTONE-593-594-FLIPPED
C12, C17: 10uF; C0805
C16: 10nF; C0805
D2, D3: MBR120; SOD-123
IC2: MPM3610; QFN-20
R4: 100K_1%; R0603
R6: 19K1_0.1%; R0603
R8: 68k; R0603

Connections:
+5V: C16.1, C17.1, IC2.7 (OUT), IC2.8 (OUT), IC2.9 (OUT), IC2.20 (OUT), R4.2; also elsewhere on the board
D5: IC2.17 (EN); also elsewhere on the board
GND: BAT.GND (-), BAT.GND1 (-), BAT.GND2 (-), C12.2, C16.2, C17.2, IC2.3 (AGND), IC2.12 (GND), IC2.13 (GND), IC2.14 (GND), R6.1, R8.1; also elsewhere on the board
unnamed: BAT.PWR (+), BAT.PWR1 (+), BAT.PWR2 (+), D3.A
unnamed: IC2.1 (FB), R4.1, R6.2
unnamed: IC2.18 (AAM), R8.2
VBAT: C12.1, D2.A, D3.C, IC2.16 (VIN)
VBUS: D2.C; also elsewhere on the board

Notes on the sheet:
Energiser Ultimate Lithium 9V in Keystone Electronics 593 and 594 clips

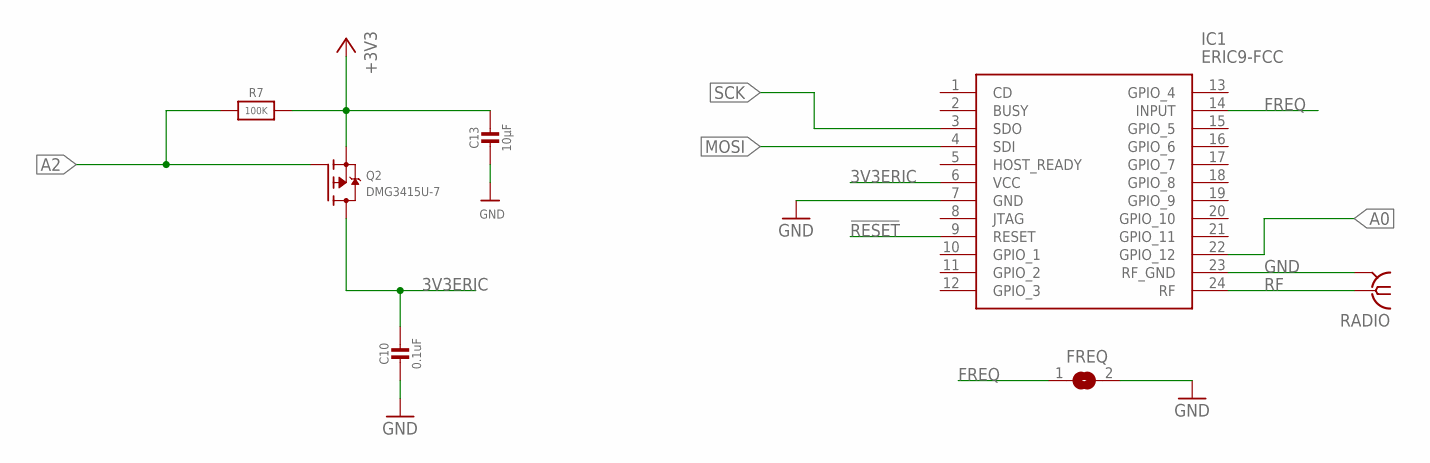
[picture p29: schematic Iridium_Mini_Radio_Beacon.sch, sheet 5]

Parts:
C10: 0.1uF; 0603-NO
C13: 10µF; 0805-NO
FREQ: SOLDERJUMPER; SOLDERJUMPER_ARROW_NOPASTE
IC1: ERIC9-FCC; ERIC4
Q2: DMG3415U-7; SOT23-WIDE
R7: 100K; 0603-NO
RADIO: SMA-142-0711-821/826; J502-ND-142-0711-821/826

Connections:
3V3ERIC: C10.1, IC1.6 (VCC), Q2.3 (D)
!RESET: IC1.9 (RESET); also elsewhere on the board
+3V3: C13.1, Q2.2 (S), R7.2; also elsewhere on the board
A0: IC1.22 (GPIO_12); also elsewhere on the board
A2: Q2.1 (G), R7.1; also elsewhere on the board
FREQ: FREQ.1, IC1.14 (INPUT)
GND: C10.2, C13.2, FREQ.2, IC1.7 (GND), IC1.23 (RF_GND), RADIO.G@1 (2), RADIO.G@2 (2), RADIO.G@3 (2), RADIO.G@4 (2); also elsewhere on the board
MOSI: IC1.4 (SDI); also elsewhere on the board
RF: IC1.24 (RF), RADIO.1
SCK: IC1.3 (SDO); also elsewhere on the board

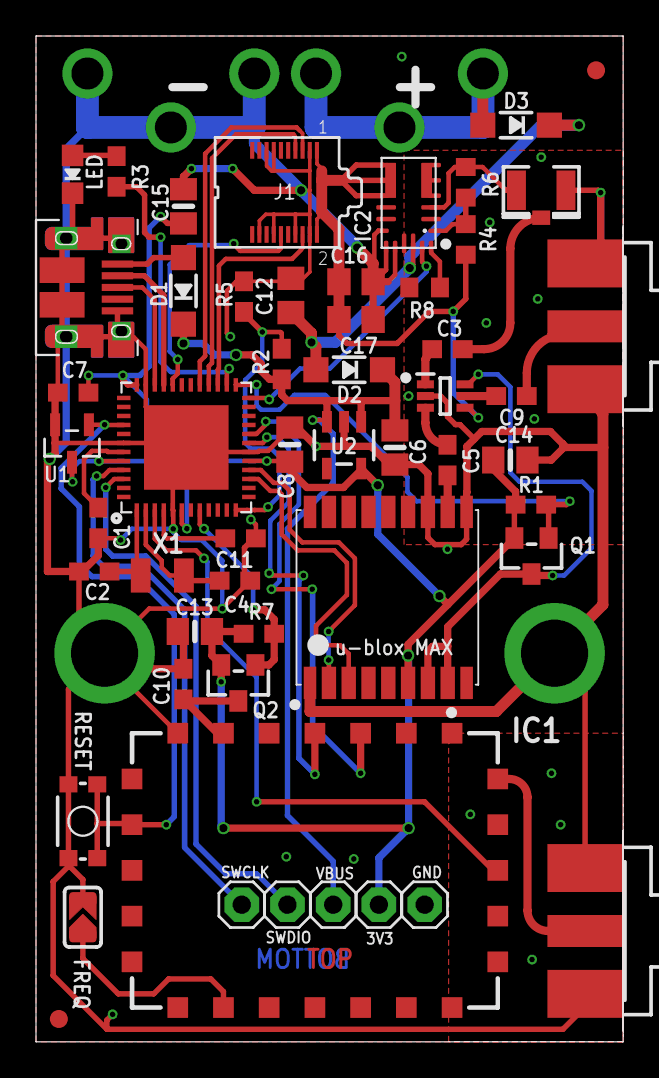
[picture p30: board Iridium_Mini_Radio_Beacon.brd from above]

Board: 2 copper layers, 32.6 x 55.9 mm, 56 parts (1 on the bottom side), 43 nets.

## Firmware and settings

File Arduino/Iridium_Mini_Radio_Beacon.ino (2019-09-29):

// ###################################
// # Iridium 9603N Mini Radio Beacon #
// ###################################

// Stores both source and destination RockBLOCK serial numbers in flash.
// The default values are:
#define RB_destination 0 // Serial number of the destination RockBLOCK (int). Set to zero to disable RockBLOCK message forwarding
#define RB_source 0 // Serial number of this unit (int)

// Define how often messages are sent in MINUTES (max 1440)
// This is the _quickest_ messages will be sent. Could be much slower than this depending on:
// capacitor charge time; gnss fix time; Iridium timeout; etc.
// The default value will be overwritten with the one stored in Flash - if one exists
// The value can be changed via a Mobile Terminated message
int BEACON_INTERVAL = 5;

// GNSS / Iridium antenna switching is via a Skyworks AS179-92LF RF Switch
// Switching is performed by applying either +5V or 3V3SW to the AS179's V1 and V2 pins
// +5V is the power rail for the 9603N from the MPM3610 (enabled by pulling D5 high)
// 3V3SW is the 3.3V power rail for the MAX-M8Q (switched via Q1, enabled by pulling D11 low)
// Take great care to make sure +5V and 3V3SW are not enabled at the same time!
// BADS THINGS WILL PROBABLY HAPPEN IF YOU DO ENABLE BOTH SIMULTANEOUSLY!

// Uses Cristian Maglie's FlashStorage library to store the BEACON_INTERVAL setting
// https://github.com/cmaglie/FlashStorage
// BEACON_INTERVAL can be updated via an Iridium Mobile Terminated message (e.g. from RockBLOCK Operations or a Beacon Base)

// With grateful thanks to Mikal Hart:
// Based on Mikal's IridiumSBD Beacon example: https://github.com/mikalhart/IridiumSBD
// Requires Mikal's TinyGPS library: https://github.com/mikalhart/TinyGPS
// and PString: http://arduiniana.org/libraries/pstring/

// With grateful thanks to:
// Adafruit: https://learn.adafruit.com/using-atsamd21-sercom-to-add-more-spi-i2c-serial-ports/creating-a-new-serial
// MartinL: https://forum.arduino.cc/index.php?topic=341054.msg2443086#msg2443086

// The Iridium_9603_Beacon PCB is based on the Adafruit Feather M0 (Adalogger)
// https://www.adafruit.com/products/2796
// GPS data provided by u-blox MAX-M8Q
// https://www.u-blox.com/en/product/max-m8-series

// Uses RTCZero to provide sleep functionality (on the M0)
// https://github.com/arduino-libraries/RTCZero

// With grateful thanks to CaveMoa for his SimpleSleepUSB example
// https://github.com/cavemoa/Feather-M0-Adalogger
// https://github.com/cavemoa/Feather-M0-Adalogger/tree/master/SimpleSleepUSB
// Note: you will need to close and re-open your serial monitor each time the M0 wakes up

// With thanks to David A. Mellis and Tom Igoe for the smoothing tutorial
// http://www.arduino.cc/en/Tutorial/Smoothing

// This version provides support for the LPRS eRIC4/9
// eRIC Pin4 Tx (input) is connected to MOSI (Digital Pin 23, Port B Pin 10, SERCOM4 Pad 2, Serial3 Tx)
// eRIC Pin3 Rx (output) is connected to SCK (Digital Pin 24, Port B Pin 11, SERCOM4 Pad 3, Serial3 Rx)
// eRIC Pin22 (wake from low power) is connected to A0 (Digital Pin 14)
// Power for the eRIC is switched via a FET. Pull A2 (Digital Pin 16) low to enable the eRIC.
// The message to be transmitted by the radio board should be sent in an Iridium Mobile Terminated message
// (e.g. from RockBLOCK Operations or a Beacon Base) containing [RADIO=nnnnnnnn] where "nnnnnnnn" is
// the radio message (usually the serial number of the eRIC on a Pyro Cut-Down)

// Iridium 9603N is interfaced to M0 using Serial2
// D6 (Port A Pin 20) = Enable (Sleep) : Connect to 9603 ON/OFF Pin 5
// D10 (Port A Pin 18) = Serial2 TX : Connect to 9603 Pin 6
// D12 (Port A Pin 19) = Serial2 RX : Connect to 9603 Pin 7
// SCL / D21 (Port A Pin 23) = Ring Indicator : Connect to 9603 Pin 12

// Power to the 9603N is provided by an MPM3610 5V regulator
// The regulator is enabled by pulling pin D5 high

// MAX-M8Q GNSS is interfaced to M0 using Serial1
// D1 (Port A Pin 10) = Serial1 TX : Connect to GPS RX
// D0 (Port A Pin 11) = Serial1 RX : Connect to GPS TX
// D11 (Port A Pin 16) = GPS ENable : Connect to GPS EN(ABLE)

// D13 (Port A Pin 17) = Red LED
// D9 (Port A Pin 7) = AIN 7 : Bus Voltage / 2

// Red LED on D13 shows when the SAMD is in bootloader mode (LED will fade up/down)

// If you bought your 9603N from Rock7, you can have your messages delivered to another RockBLOCK automatically:
// https://www.rock7.com/shop-product-detail?productId=50
// http://www.rock7mobile.com/products-rockblock-9603
// http://www.rock7mobile.com/downloads/RockBLOCK-9603-Developers-Guide.pdf (see last page)
// Change RB_destination (above) to the serial number of the destination RockBLOCK
// Change RB_source (above) to the serial number of this RockBLOCK
// Both RBSOURCE and RBDESTINATION can be updated via a MT message.
// Note: the RockBLOCK gateway does not remove the destination RockBLOCK address from the SBD message
// so, in this code, it is included as a full CSV field

#include <IridiumSBD.h> // Requires V2: https://github.com/mikalhart/IridiumSBD
#include <TinyGPS.h> // NMEA parsing: http://arduiniana.org
#include <PString.h> // String buffer formatting: http://arduiniana.org

#include <RTCZero.h> // M0 Real Time Clock
RTCZero rtc; // Create an rtc object

// Flash Storage
#include <FlashStorage.h>
typedef struct { // Define a struct to hold the flash variable(s)
  int PREFIX; // Flash storage prefix (0xB5); used to test if flash has been written to before 
  int INTERVAL; // Message interval in minutes
  // RockBLOCK source serial number: stored as an int; i.e. the RockBLOCK serial number of the 9603N attached to this beacon
  int RBSOURCE; 
  // RockBLOCK destination serial number: stored as an int; i.e. the RockBLOCK serial number of the 9603N you would like the messages delivered _to_
  int RBDESTINATION; // Set this to zero to disable RockBLOCK gateway message forwarding
  int CSUM; // Flash storage checksum; the modulo-256 sum of PREFIX and INTERVAL; used to check flash data integrity
} FlashVarsStruct;
FlashStorage(flashVarsMem, FlashVarsStruct); // Reserve memory for the flash variables
FlashVarsStruct flashVars; // Define the global to hold the variables
int RBSOURCE = RB_source;
int RBDESTINATION = RB_destination;

// Serial2 pin and pad definitions (in Arduino files Variant.h & Variant.cpp)
#define PIN_SERIAL2_RX       (34ul)               // Pin description number for PIO_SERCOM on D12
#define PIN_SERIAL2_TX       (36ul)               // Pin description number for PIO_SERCOM on D10
#define PAD_SERIAL2_TX       (UART_TX_PAD_2)      // SERCOM pad 2 (SC1PAD2)
#define PAD_SERIAL2_RX       (SERCOM_RX_PAD_3)    // SERCOM pad 3 (SC1PAD3)
// Instantiate the Serial2 class
Uart Serial2(&sercom1, PIN_SERIAL2_RX, PIN_SERIAL2_TX, PAD_SERIAL2_RX, PAD_SERIAL2_TX);
HardwareSerial &ssIridium(Serial2);

// Serial3 pin and pad definitions (in Arduino files Variant.h & Variant.cpp)
// eRIC Tx (input) is connected to MOSI (Digital Pin 23, Port B Pin 10, SERCOM4 Pad 2, Serial3 Tx)
// eRIC Rx (output) is connected to SCK (Digital Pin 24, Port B Pin 11, SERCOM4 Pad 3, Serial3 Rx)
#define PIN_SERIAL3_RX       (24ul)               // Pin description number for PIO_SERCOM on D24
#define PIN_SERIAL3_TX       (23ul)               // Pin description number for PIO_SERCOM on D23
#define PAD_SERIAL3_TX       (UART_TX_PAD_2)      // SERCOM4 Pad 2 (SC4PAD2)
#define PAD_SERIAL3_RX       (SERCOM_RX_PAD_3)    // SERCOM4 Pad 3 (SC4PAD3)
// Instantiate the Serial3 class
Uart Serial3(&sercom4, PIN_SERIAL3_RX, PIN_SERIAL3_TX, PAD_SERIAL3_RX, PAD_SERIAL3_TX);
HardwareSerial &sseRIC(Serial3);

#define ssGPS Serial1 // Use M0 Serial1 to interface to the MAX-M8Q

// Leave the "#define GALILEO" uncommented to use: GPS + Galileo + GLONASS + SBAS
// Comment the "#define GALILEO" out to use the default u-blox M8 GNSS: GPS + SBAS + QZSS + GLONASS
#define GALILEO

// Set Nav Mode to Portable
static const uint8_t setNavPortable[] = {
  0xB5, 0x62, 0x06, 0x24, 0x24, 0x00, 0xFF, 0xFF, 0x00, 0x03, 0x00, 0x00, 0x00, 0x00, 0x10, 0x27, 0x00, 0x00, 
  0x05, 0x00, 0xFA, 0x00, 0xFA, 0x00, 0x64, 0x00, 0x2C, 0x01, 0x00, 0x00, 0x00, 0x00, 0x00, 0x00, 0x00, 0x00, 
  0x00, 0x00, 0x00, 0x00, 0x00, 0x00 };

// Set Nav Mode to Pedestrian
static const uint8_t setNavPedestrian[] = {
  0xB5, 0x62, 0x06, 0x24, 0x24, 0x00, 0xFF, 0xFF, 0x03, 0x03, 0x00, 0x00, 0x00, 0x00, 0x10, 0x27, 0x00, 0x00, 
  0x05, 0x00, 0xFA, 0x00, 0xFA, 0x00, 0x64, 0x00, 0x2C, 0x01, 0x00, 0x00, 0x00, 0x00, 0x00, 0x00, 0x00, 0x00, 
  0x00, 0x00, 0x00, 0x00, 0x00, 0x00 };

// Set Nav Mode to Automotive
static const uint8_t setNavAutomotive[] = {
  0xB5, 0x62, 0x06, 0x24, 0x24, 0x00, 0xFF, 0xFF, 0x04, 0x03, 0x00, 0x00, 0x00, 0x00, 0x10, 0x27, 0x00, 0x00, 
  0x05, 0x00, 0xFA, 0x00, 0xFA, 0x00, 0x64, 0x00, 0x2C, 0x01, 0x00, 0x00, 0x00, 0x00, 0x00, 0x00, 0x00, 0x00, 
  0x00, 0x00, 0x00, 0x00, 0x00, 0x00 };

// Set Nav Mode to Sea
static const uint8_t setNavSea[] = {
  0xB5, 0x62, 0x06, 0x24, 0x24, 0x00, 0xFF, 0xFF, 0x05, 0x03, 0x00, 0x00, 0x00, 0x00, 0x10, 0x27, 0x00, 0x00, 
  0x05, 0x00, 0xFA, 0x00, 0xFA, 0x00, 0x64, 0x00, 0x2C, 0x01, 0x00, 0x00, 0x00, 0x00, 0x00, 0x00, 0x00, 0x00, 
  0x00, 0x00, 0x00, 0x00, 0x00, 0x00 };

// Set Nav Mode to Airborne <1G
static const uint8_t setNavAir[] = {
  0xB5, 0x62, 0x06, 0x24, 0x24, 0x00, 0xFF, 0xFF, 0x06, 0x03, 0x00, 0x00, 0x00, 0x00, 0x10, 0x27, 0x00, 0x00, 
  0x05, 0x00, 0xFA, 0x00, 0xFA, 0x00, 0x64, 0x00, 0x2C, 0x01, 0x00, 0x00, 0x00, 0x00, 0x00, 0x00, 0x00, 0x00, 
  0x00, 0x00, 0x00, 0x00, 0x00, 0x00 };

static const int len_setNav = 42;

// Set NMEA Config
// Set trackFilt to 1 to ensure course (COG) is always output
// Set Main Talker ID to 'GP' to avoid having to modify TinyGPS
static const uint8_t setNMEA[] = {
  0xb5, 0x62, 0x06, 0x17, 0x14, 0x00, 0x20, 0x40, 0x00, 0x02, 0x00, 0x00, 0x00, 0x00, 0x00, 0x01, 0x01, 0x01,
  0x00, 0x00, 0x00, 0x00, 0x00, 0x00, 0x00, 0x00 };
static const int len_setNMEA = 26;

// Set GNSS Config to GPS + Galileo + GLONASS + SBAS (Causes the M8 to restart!)
static const uint8_t setGNSS[] = {
  0xb5, 0x62, 0x06, 0x3e, 0x3c, 0x00,
  0x00, 0x20, 0x20, 0x07,
  0x00, 0x08, 0x10, 0x00, 0x01, 0x00, 0x01, 0x01,
  0x01, 0x01, 0x03, 0x00, 0x01, 0x00, 0x01, 0x01,
  0x02, 0x04, 0x08, 0x00, 0x01, 0x00, 0x01, 0x01,
  0x03, 0x08, 0x10, 0x00, 0x00, 0x00, 0x01, 0x01,
  0x04, 0x00, 0x08, 0x00, 0x00, 0x00, 0x01, 0x03,
  0x05, 0x00, 0x03, 0x00, 0x00, 0x00, 0x01, 0x05,
  0x06, 0x08, 0x0e, 0x00, 0x01, 0x00, 0x01, 0x01 };
static const int len_setGNSS = 66;

static const int Enable_9603N = 5; // Enables the MPM3610 to provide power for the 9603N
static const int ringIndicator = 21; // 9603 Ring Indicator on pin D21
static const int IridiumSleepPin = 6; // Iridium Sleep connected to D6
IridiumSBD isbd(ssIridium, IridiumSleepPin); // This should disable the 9603
TinyGPS tinygps;
long iterationCounter = 0; // Increment each time a transmission is attempted

static const int ledPin = 13; // WB2812B + Red LED on pin D13
//#define NoLED // Uncomment this line to disable the LED

static const int GPS_EN = 11; // GNSS Enable on pin D11
#define GPS_ON LOW
#define GPS_OFF HIGH
#define VAP A7 // Bus voltage analog pin (bus voltage divided by 2)
#define VBAT_LOW 5.0 // Minimum voltage for MPM3610 less one MBR120 voltage drop

// eRIC Pin22 (wake from low power) is connected to A0 (Digital Pin 14)
static const int eRIC_WAKE = 14;
// A2 (Digital Pin 16) enables power for the eRIC
static const int eRIC_EN = 16;

// Loop Steps
#define init          0
#define start_GPS     1
#define read_GPS      2
#define start_9603    3
#define zzz           4
#define wake          5

// Variables used by Loop
int year;
byte month, day, hour, minute, second, hundredths;
unsigned long dateFix, locationFix;
float latitude, longitude;
long altitude;
float speed;
short satellites;
long course;
long hdop;
bool fixFound = false;
bool charsSeen = false;
int loop_step = init;
float vbat = 9.0;
unsigned long tnow;

// Storage for the average voltage during Iridium callbacks
const int numReadings = 25;   // number of samples
int readings[numReadings];    // the readings from the analog input
int readIndex = 0;            // the index of the current reading
long int total = 0;           // the running total
int latest_reading = 0;       // the latest reading
int average_reading = 0;      // the average reading

// IridiumSBD Callbacks
bool ISBDCallback()
{
#ifndef NoLED
  // 'Flash' the LED
  if ((millis() / 333) % 2 == 1) {
    digitalWrite(ledPin, HIGH);
  }
  else {
    digitalWrite(ledPin, LOW);
  }
#endif

  // Check the 'battery' voltage now we are drawing current for the 9603
  // If voltage is low, stop Iridium send
  get_vbat_smooth();

  if (vbat < VBAT_LOW) {
    Serial.print("***!!! LOW VOLTAGE (ISBDCallback) ");
    Serial.print(vbat,2);
    Serial.println("V !!!***");
    return false; // Returning false causes IridiumSBD to terminate
  }
  else {     
    return true;
  }

  delay(1);
}
// V2 console and diagnostic callbacks (replacing attachConsole and attachDiags)
void ISBDConsoleCallback(IridiumSBD *device, char c) { Serial.write(c); }
void ISBDDiagsCallback(IridiumSBD *device, char c) { Serial.write(c); }

// Interrupt handler for SERCOM1 (essential for Serial2 comms)
void SERCOM1_Handler()
{
  Serial2.IrqHandler();
}

// Interrupt handler for SERCOM4 (essential for Serial3 comms)
void SERCOM4_Handler()
{
  Serial3.IrqHandler();
}

// RTC alarm interrupt
void alarmMatch()
{
  int rtc_mins = rtc.getMinutes(); // Read the RTC minutes
  int rtc_hours = rtc.getHours(); // Read the RTC hours
  if (BEACON_INTERVAL > 1440) BEACON_INTERVAL = 1440; // Limit BEACON_INTERVAL to one day
  rtc_mins = rtc_mins + BEACON_INTERVAL; // Add the BEACON_INTERVAL to the RTC minutes
  while (rtc_mins >= 60) { // If there has been an hour roll over
    rtc_mins = rtc_mins - 60; // Subtract 60 minutes
    rtc_hours = rtc_hours + 1; // Add an hour
  }
  rtc_hours = rtc_hours % 24; // Check for a day roll over
  rtc.setAlarmMinutes(rtc_mins); // Set next alarm time (minutes)
  rtc.setAlarmHours(rtc_hours); // Set next alarm time (hours)
}

// Read and smooth the 'battery' voltage
// Average voltage over numReadings to smooth out any short dips
void get_vbat_smooth() {
  // subtract the last reading:
  total = total - readings[readIndex];
  // read from the sensor:
  latest_reading = analogRead(VAP);
  readings[readIndex] = latest_reading;
  // add the reading to the total:
  total = total + latest_reading;
  // advance to the next position in the array:
  readIndex = readIndex + 1;
  // if we're at the end of the array...wrap around to the beginning:
  if (readIndex >= numReadings) readIndex = 0;
  // calculate the average:
  average_reading = total / numReadings; // Seems to work OK with integer maths - but total does need to be long int
  vbat = float(average_reading) * (4.3 * 3.3 / 1023.0); // Calculate average battery voltage
}

// Read the instantaneous 'battery' voltage
void get_vbat() {
  vbat = analogRead(VAP) * (4.3 * 3.3 / 1023.0); // Read battery voltage from resistor divider
}
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
void loop()
{
  unsigned long loopStartTime = millis();

  switch(loop_step) {

    case init:

#ifndef NoLED
      digitalWrite(ledPin, HIGH);
#endif

      // Start the serial console
      Serial.begin(115200);
      delay(5000); // Wait 5 secs - allow time for user to open serial monitor
    
      // Send welcome message
      Serial.println("Iridium 9603N Mini Radio Beacon");

      // Echo the BEACON_INTERVAL
      Serial.print("Using a BEACON_INTERVAL of ");
      Serial.print(BEACON_INTERVAL);
      Serial.println(" minutes");
      
      // Echo RBDESTINATION and RBSOURCE
      Serial.print("Using an RBDESTINATION of ");
      Serial.println(RBDESTINATION);
      Serial.print("Using an RBSOURCE of ");
      Serial.println(RBSOURCE);

      // Setup the IridiumSBD
      // (attachConsole and attachDiags methods have been replaced with ISBDConsoleCallback and ISBDDiagsCallback)
      isbd.setPowerProfile(IridiumSBD::DEFAULT_POWER_PROFILE); // Change power profile to default
      isbd.useMSSTMWorkaround(false); // Redundant?

      // Check battery voltage
      // If voltage is low, go to sleep
      init_vbat(); // Use init_vbat to make sure the current true smoothed voltage is used (after coming out of deep sleep)
      if (vbat < VBAT_LOW) {
        Serial.print("***!!! LOW VOLTAGE (init) ");
        Serial.print(vbat,2);
        Serial.println(" !!!***");
        loop_step = zzz;
      }
      else {
        loop_step = start_GPS;
      }
      
      break;
      
    case start_GPS:

      // Power up the GNSS
      Serial.println("Powering up the GNSS...");
      digitalWrite(GPS_EN, GPS_ON); // Enable the GNSS

      delay(2000); // Allow time for both to start
    
      // Check battery voltage now we are drawing current for the GPS
      // If voltage is low, go to sleep
      init_vbat(); // Use init_vbat to make sure the true smoothed voltage is used
      if (vbat < VBAT_LOW) {
        Serial.print("***!!! LOW VOLTAGE (start_GPS) ");
        Serial.print(vbat,2);
        Serial.println("V !!!***");
        loop_step = zzz;
      }
      else {
        loop_step = read_GPS;
      }
      
      break;

    case read_GPS:
      // Start the GPS serial port
      ssGPS.begin(9600);

      delay(1000); // Allow time for the port to open

      // Configure GPS
      Serial.println("Configuring GNSS...");

      // Disable all messages except GGA and RMC
      ssGPS.println("$PUBX,40,GLL,0,0,0,0*5C"); // Disable GLL
      delay(1100);
      ssGPS.println("$PUBX,40,ZDA,0,0,0,0*44"); // Disable ZDA
      delay(1100);
      ssGPS.println("$PUBX,40,VTG,0,0,0,0*5E"); // Disable VTG
      delay(1100);
      ssGPS.println("$PUBX,40,GSV,0,0,0,0*59"); // Disable GSV
      delay(1100);
      ssGPS.println("$PUBX,40,GSA,0,0,0,0*4E"); // Disable GSA
      delay(1100);
      
      //sendUBX(setNavPortable, len_setNav); // Set Portable Navigation Mode
      //sendUBX(setNavPedestrian, len_setNav); // Set Pedestrian Navigation Mode
      //sendUBX(setNavAutomotive, len_setNav); // Set Automotive Navigation Mode
      //sendUBX(setNavSea, len_setNav); // Set Sea Navigation Mode
      sendUBX(setNavAir, len_setNav); // Set Airborne <1G Navigation Mode
      delay(1100);

      sendUBX(setNMEA, len_setNMEA); // Set NMEA: to always output COG; and set main talker to GP (instead of GN)
      delay(1100);

#ifdef GALILEO
      sendUBX(setGNSS, len_setGNSS); // Set GNSS - causes M8 to restart!
      delay(3000); // Wait an extra time for GNSS to restart
#endif

      while(ssGPS.available()){ssGPS.read();} // Flush RX buffer so we don't confuse TinyGPS with UBX acknowledgements

      // Reset TinyGPS and begin listening to the GNSS
      Serial.println("Beginning to listen for GNSS traffic...");
      fixFound = false; // Reset fixFound
      charsSeen = false; // Reset charsSeen
      tinygps = TinyGPS();
      
      // Look for GPS signal for up to 5 minutes
      for (tnow = millis(); !fixFound && millis() - tnow < 5UL * 60UL * 1000UL;)
      {
        if (ssGPS.available())
        {
          charsSeen = true;
          if (tinygps.encode(ssGPS.read()))
          {
            tinygps.f_get_position(&latitude, &longitude, &locationFix);
            tinygps.crack_datetime(&year, &month, &day, &hour, &minute, &second, &hundredths, &dateFix);
            altitude = tinygps.altitude(); // Altitude in cm (long) - checks that we have received a GGA message
            speed = tinygps.f_speed_mps(); // Get speed - checks that we have received an RMC message
            satellites = tinygps.satellites(); // Get number of satellites
            course = tinygps.course(); // Get course over ground
            hdop = tinygps.hdop(); // Get horizontal dilution of precision
            fixFound = locationFix != TinyGPS::GPS_INVALID_FIX_TIME && 
                       dateFix != TinyGPS::GPS_INVALID_FIX_TIME && 
                       altitude != TinyGPS::GPS_INVALID_ALTITUDE &&
                       speed != TinyGPS::GPS_INVALID_F_SPEED &&
                       satellites != TinyGPS::GPS_INVALID_SATELLITES &&
                       course != TinyGPS::GPS_INVALID_ANGLE &&
                       hdop != TinyGPS::GPS_INVALID_HDOP &&
                       year != 2000;
          }
        }

        // if we haven't seen any GPS data in 10 seconds, then stop waiting
        if (!charsSeen && millis() - tnow > 10000) {
          break;
        }

        // Check battery voltage now we are drawing current for the GPS
        // If voltage is low, stop looking for GNSS and go to sleep
        get_vbat_smooth();
        if (vbat < VBAT_LOW) {
          break;
        }

#ifndef NoLED
        // 'Flash' the LED
        if ((millis() / 1000) % 2 == 1) {
          digitalWrite(ledPin, HIGH);
        }
        else {
          digitalWrite(ledPin, LOW);
        }
#endif

      }

      Serial.println(charsSeen ? fixFound ? F("A GNSS fix was found!") : F("No GNSS fix was found.") : F("Wiring error: No GNSS data seen."));
      Serial.print("Latitude (degrees): "); Serial.println(latitude, 6);
      Serial.print("Longitude (degrees): "); Serial.println(longitude, 6);
      Serial.print("Altitude (m): "); Serial.println(altitude / 100); // Convert altitude from cm to m

      if (vbat < VBAT_LOW) {
        Serial.print("***!!! LOW VOLTAGE (read_GNSS) ");
        Serial.print(vbat,2);
        Serial.println("V !!!***");
        loop_step = zzz;
      }
      else if (!charsSeen) {
        Serial.println("***!!! No GNSS data received !!!***");
        loop_step = zzz;
      }
      else {
        // Power down the GNSS
        Serial.println("Powering down the GNSS...");
        digitalWrite(GPS_EN, GPS_OFF); // Disable the GPS
        delay(1000); // Let the voltage decay
        loop_step = start_9603;
      }
      
      break;

    case start_9603:
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

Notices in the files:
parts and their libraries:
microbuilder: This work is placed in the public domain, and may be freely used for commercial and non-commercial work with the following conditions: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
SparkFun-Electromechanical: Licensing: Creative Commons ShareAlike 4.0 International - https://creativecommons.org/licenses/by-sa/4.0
